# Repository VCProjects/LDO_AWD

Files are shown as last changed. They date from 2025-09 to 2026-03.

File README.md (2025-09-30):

# LDO CNC AWD Kit <sub>by Mastur_Mynd and aTinyShellScript</sub>
CNC drive frames for the [Voron Trident](https://github.com/VoronDesign/Voron-Trident) and [Voron V2.4](https://github.com/VoronDesign/Voron-2)

VT_rear_b_outer

## Key Features
* Metal! - Improved heat dissipation of stepper motors at higher current
* Shorter effective belt length between toolhead and drive gear - Improves max acceleration, input shaper results and accuracy during direction change.
* Double shear shaft support - Allows for increased tension without deflecting the drive shaft
* Backwards compatible - Toolheads or XY joints designed for the Voron Trident or Voron V2.4 will work! Keep in mind that different toolhead geometries may result in loss of travel near the front motor mounts.
* (Voron V2.4 only) Live shaft idlers - Like toothed idlers but utilizing more robust bearings for longevity

## Vendors
* [DREMC (AU)](https://store.dremc.com.au/products/ldo-voron-cnc-awd-kit-v2-4-trident)
* [3d lab tech (CA)](https://www.3dlabtech.ca/)
* [MYRIGS (FR)](https://myrigs3d.com/products/ldo-cnc-all-wheel-drive-kit-for-voron-v2-4-and-trident)
* [Partner 3D (GE)](https://partner-3d.de/)
* [Levendigs (NE)](https://levendigs.com/)
* [onetwo3D (UK)](https://www.onetwo3d.co.uk/product/ldo-voron-awd-all-wheel-drive-upgrade-kit/)
* [123-3D (UK)](https://www.123-3d.co.uk/) subsidiary of [H|2|E Commerce](https://h2ecommerce.com/)
* [Fabreeko (US)](https://www.fabreeko.com/products/ldo-cnc-all-wheel-drive-kit-for-voron-v2-4-and-trident)
* KB3D (US) [Voron Trident](https://kb-3d.com/store/voron/6134-pre-order-ldo-cnc-awd-conversion-kit-for-voron-trident-1757455457877.html) [Voron V2.4](https://kb-3d.com/store/motion/6133-pre-order-ldo-cnc-awd-conversion-kit-for-voron-v24-1757455457079.html)
* [West3D (US)](https://west3d.com/products/ldo-voron-cnc-awd-kit-v2-4-or-trident)

This kit was designed and tested in collaboration with LDO Motors. Kits produced by other manufacturers have not been vetted and may not have the same standard of quality.

## Belt Tensioning
While not required, ensuring your A and B belts are the same length will make tensioning easier.

1. Home your printer. `G28`
	* For the Voron V2 you will also need to perform a quad gantry level. `QUAD_GANTRY_LEVEL`
2. Raise the toolhead (or lower the bed) to prevent the nozzle from marring the build surface. `G0 Z+25`
3. Disable your A and B motors
   ```
   SET_STEPPER_ENABLE STEPPER=stepper_x ENABLE=0
   SET_STEPPER_ENABLE STEPPER=stepper_x1 ENABLE=0
   SET_STEPPER_ENABLE STEPPER=stepper_y ENABLE=0
   SET_STEPPER_ENABLE STEPPER=stepper_y1 ENABLE=0
   ```
4. Loosen the grub screws holding the front drive pulleys to the motor shaft. Ensure that the pulleys are able to move freely from the shaft.
5. Move your toolhead to the center of the bed
6. Adjust tension on each belt path using the M5 SHCS in the tensioner block. Try to adjust tension evenly across the two belt paths, reducing adjustments as you get closer to your desired tension
7. Move the toolhead in the X and Y directions to make sure it is moving freely.
8. Enable your A and B motors. This will send them to the nearest full step which will sync the motors and pulleys in the next step.
   ```
   SET_STEPPER_ENABLE STEPPER=stepper_x ENABLE=1
   SET_STEPPER_ENABLE STEPPER=stepper_x1 ENABLE=1
   SET_STEPPER_ENABLE STEPPER=stepper_y ENABLE=1
   SET_STEPPER_ENABLE STEPPER=stepper_y1 ENABLE=1
   ```
9. Tighten the grub screws holding the front drive pulleys to the motor shaft. Ensure that none of the grub screws are along the flat when using a D cut shaft motor.

## Credit and Attribution
**Lead Designer**\
Mastur_Mynd

**Lead Design Consultant**\
aTinyShellScript

**Project Coordinator**\
JasonFromLDO

**Design Consultant**\
CameronFromLDO\
DaveFromLDO

**Production**\
LDO Motors

**Testing**\
hartk\
JoseFromLDO us\
joshmurrah\
Kittie Katt\
Reth\
ThessienDSD

**Base Design**\
Voron Design Team

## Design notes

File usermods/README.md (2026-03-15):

# Mods by users - For users
This section houses creations from users that have either made assembly easier, improved functionality or just look too-darn-cool!

## Requirements
* All mods must abide by GPLv3 licensing standards. This means the CAD document (preferably .STEP format) must be included along with printable STL files. Additionally, attribution must be provided if an external source file was used (all mods here are assumed to derrive from the kits, no attribution to these kits are necessary).
* All STL files are expected to be print ready, meaning their orientation should not need to change after importing into the users' preferred slicer.
* Include some images of the finished product. This can either be a render or a photo of a printed part
* Include a BOM (bill of materials) and note whether or not the required hardware was already included in the kit.
* If the mod changes, removes, or improves functionality, please describe how it does so
* If the mod is a complex change you'll need to include documentation in some form on how to install your mod.
* Kit compatability should use the following: `:heavy_check_mark:` for compatible,`:x:` for NOT compatible and `:grey_question:` for unknown compatability

| Author | Mod Name | V2 AWD | V2 2WD | VT AWD | VT 2WD |
|---|---|---|---|---|---|
| Mastur_Mynd | [Y Endstop Mount](./Mastur_Mynd/Y_Endstop_Mount) | :heavy_check_mark: | :heavy_check_mark: | :heavy_check_mark: | :heavy_check_mark: |
| Kyle_GB| [Accent Sleeves](./Kyle_GB/Accent_Sleeves) | :heavy_check_mark: | :heavy_check_mark: | :heavy_check_mark: | :heavy_check_mark: |
| TheSin- | [AABB Microfit3 Pods](./TheSin-/AABB_Microfit3_Pods) | :heavy_check_mark: | :x: | :x: | :x: |
| TheSin- | [Front Motor Wiring](./TheSin-/Front_Motor_Wiring) | :heavy_check_mark: | :x: | :x: | :x: |
| TheSin- | [Zumbilical](./TheSin-/Zumbilical) | :heavy_check_mark: | :heavy_check_mark: | :x: | :x: |

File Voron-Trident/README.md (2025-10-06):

# LDO CNC AWD Kit <sub>by Mastur_Mynd and aTinyShellScript</sub>
CNC drive frames designed specifically for your [Voron Trident](https://github.com/VoronDesign/Voron-Trident)

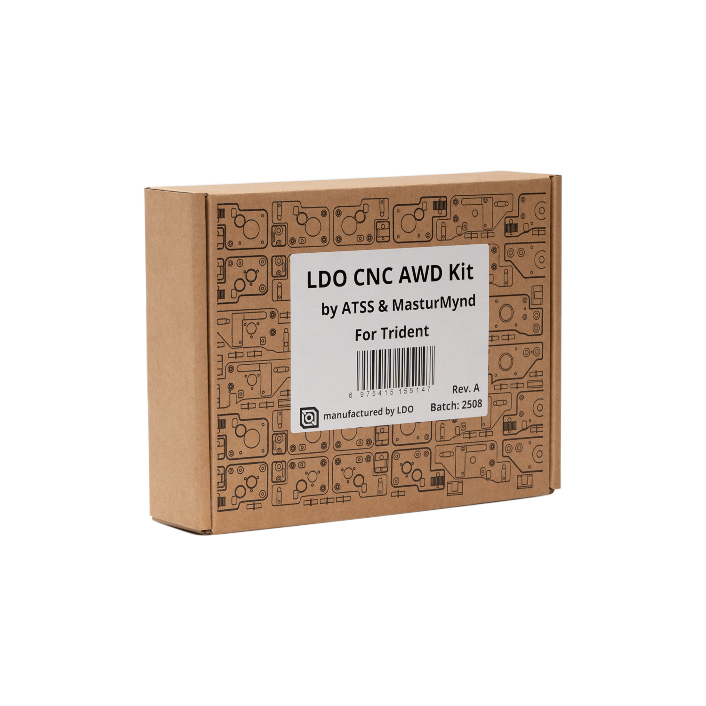
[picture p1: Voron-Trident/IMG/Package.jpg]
Package


## Things to consider
There are a few printed parts recommended for clean cable management. Head over to the STL directory to download these files and print what you'll need before prepping for installation.

It is recommended to get some channel covers for your front corner extrusions to hide the front motor wires on their way to the electronics bay.

Depending on the orientation of the front motor mounts and the toolhead assembly, some amount of printable area will be lost at the front corners of the build plate. The below table will be updated as data comes in. If you would like to contribute to this table please submit a pull request or create an issue with dimensions for both the Voron Trident and the Voron V2.4r2.

---
| Toolhead | X Loss (mm) | Y Loss (mm) |
| --- | --- | --- |
| Stealthburner | 17.8 | 47.6 |

## So what's in the box?!
Note that the Contents section of the [assembly manual](assembly_manual.pdf) accounts for individual hardware components. For an improved assembly experience some components are preinstalled.

---
| Qty | Part Name | Image |
| --- | --- | --- |
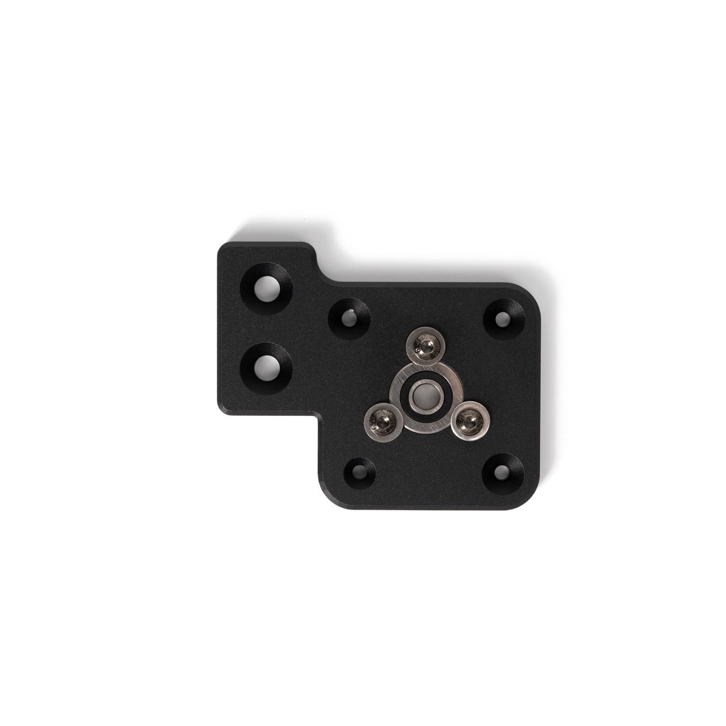
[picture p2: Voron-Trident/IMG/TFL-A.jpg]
TFL-A
| 1 | Front A Drive Frame Lower |  |
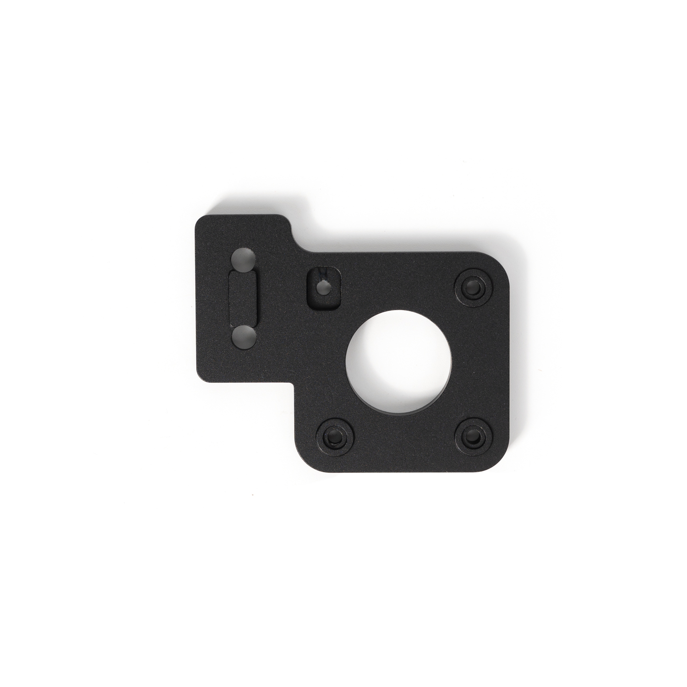
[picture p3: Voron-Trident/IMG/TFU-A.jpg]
TFU-A
| 1 | Front A Drive Frame Upper |  |
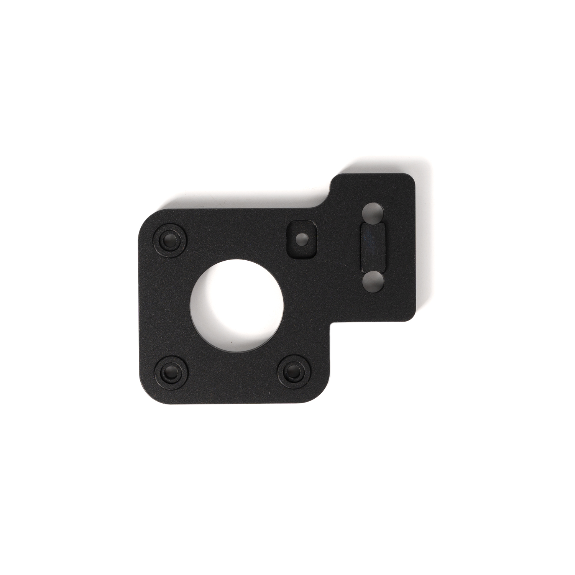
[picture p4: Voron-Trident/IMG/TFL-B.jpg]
TFL-B
| 1 | Front B Drive Frame Lower |  |
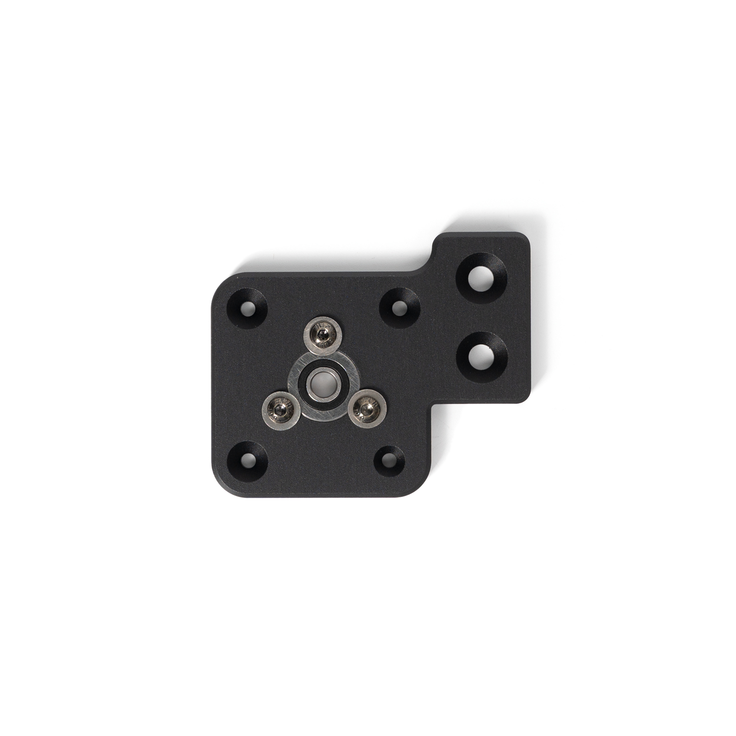
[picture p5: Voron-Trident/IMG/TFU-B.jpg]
TFU-B
| 1 | Front B Drive Frame Upper |  |
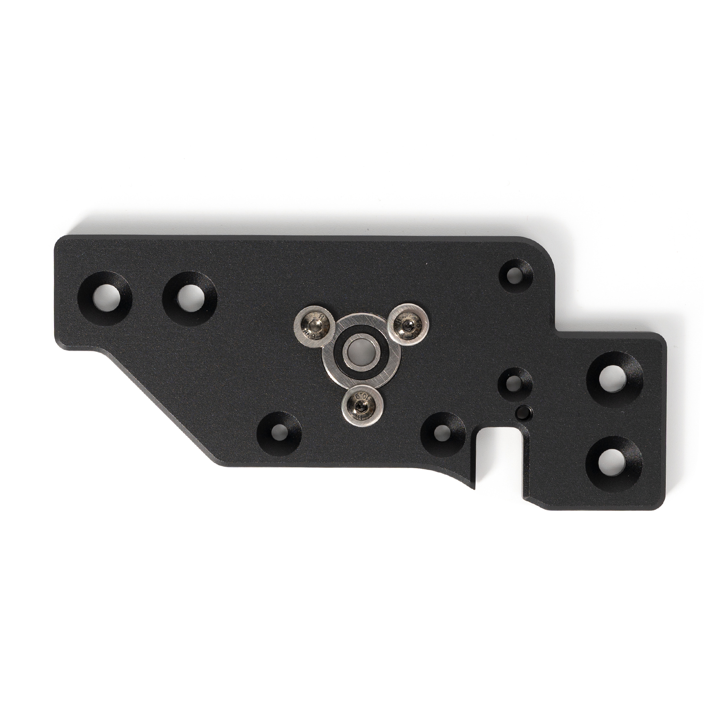
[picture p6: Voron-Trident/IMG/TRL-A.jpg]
TRL-A
| 1 | Rear A Drive Frame Lower |  |
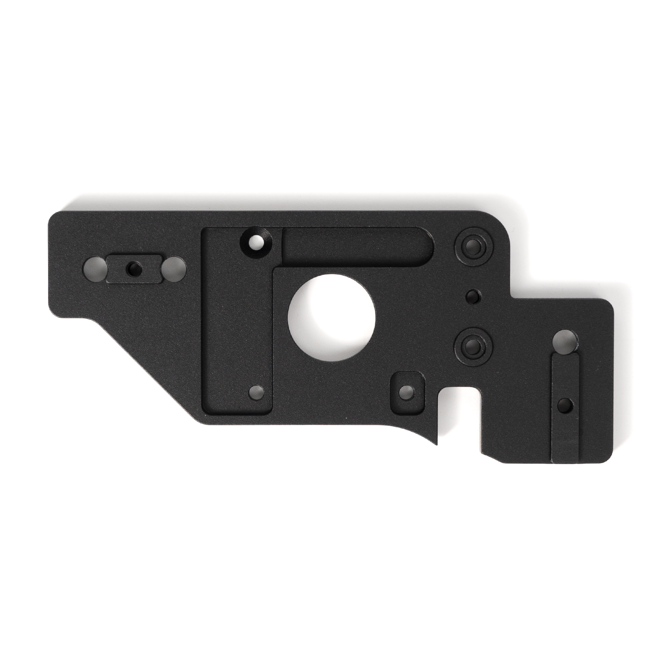
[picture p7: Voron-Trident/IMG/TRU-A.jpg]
TRU-A
| 1 | Rear A Drive Frame Upper |  |
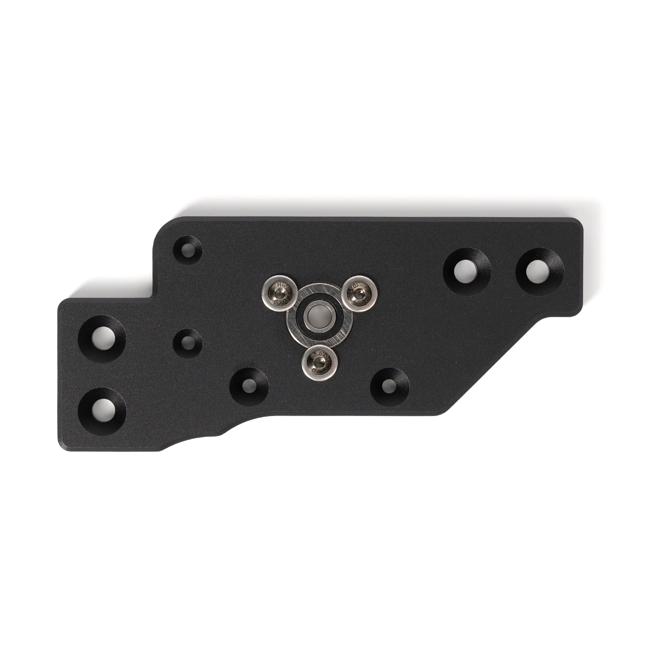
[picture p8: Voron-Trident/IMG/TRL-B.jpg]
TRL-B
| 1 | Rear B Drive Frame Lower |  |
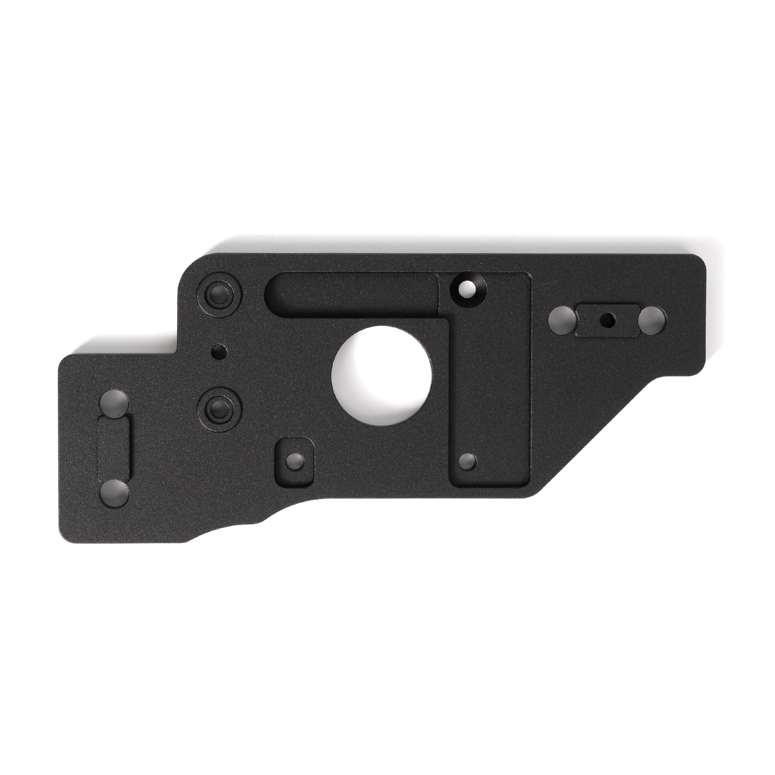
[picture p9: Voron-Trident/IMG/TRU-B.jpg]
TRU-B
| 1 | Rear B Drive Frame Upper |  |
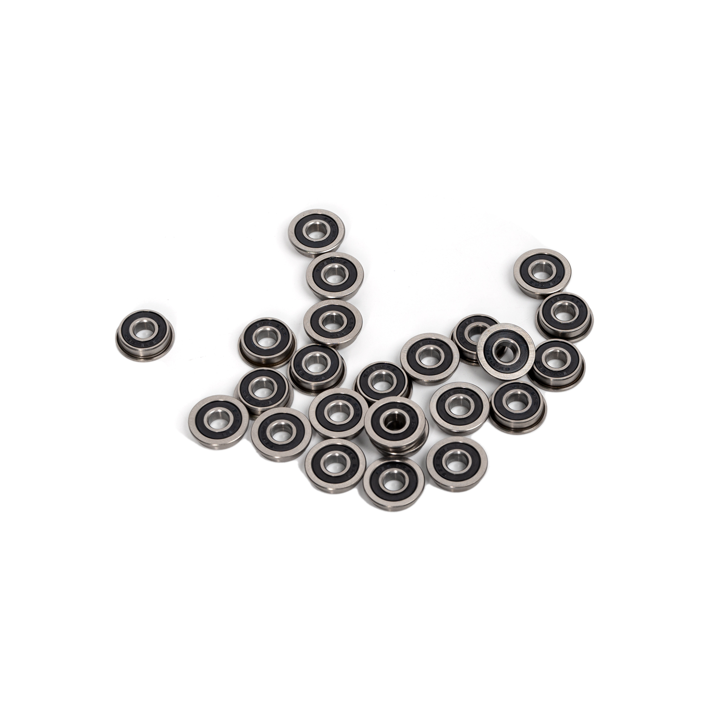
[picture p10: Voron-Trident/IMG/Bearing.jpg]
Bearing
| 24 | F695-2RS Bearing |  |
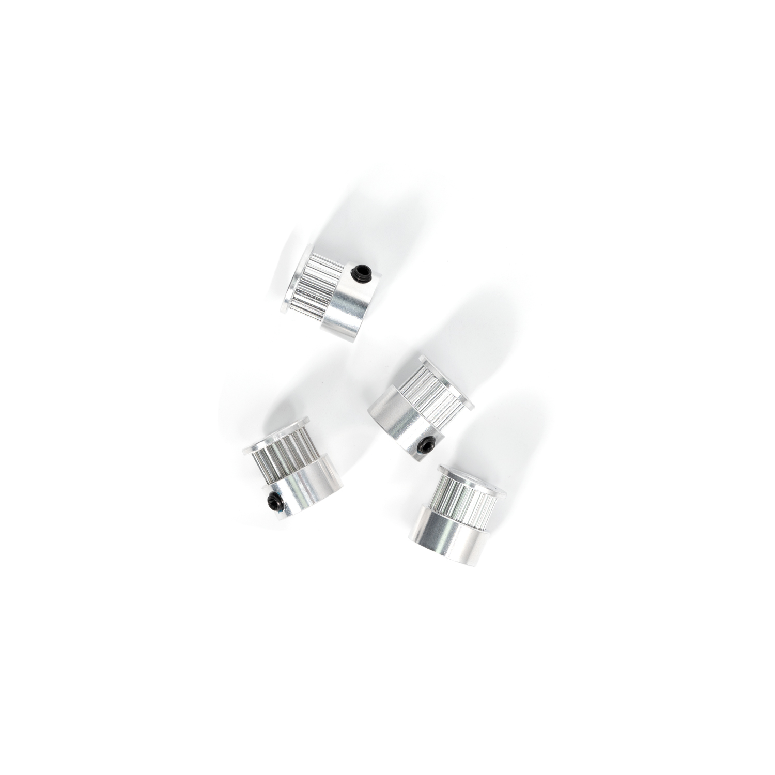
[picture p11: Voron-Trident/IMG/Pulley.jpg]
Pulley
| 4 | Pulley |  |
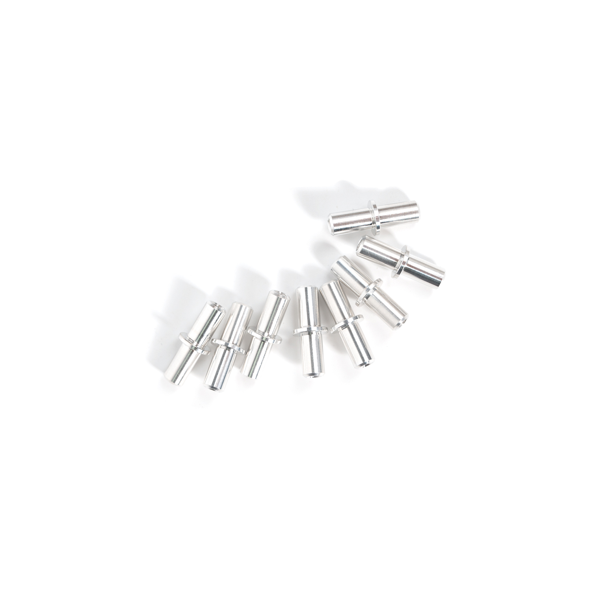
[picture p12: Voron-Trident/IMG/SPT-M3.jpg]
SPT-M3
| 8 | Shim Pin - Threaded (M3) |  |
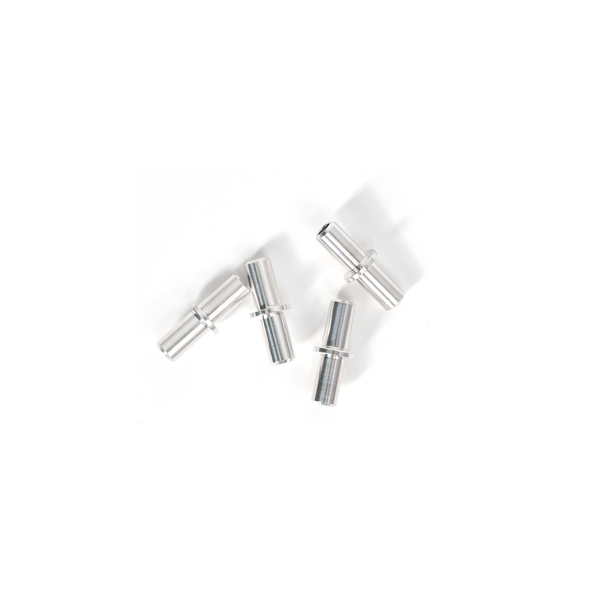
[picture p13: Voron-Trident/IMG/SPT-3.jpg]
SPT-3
| 4 | Shim Pin - Unthreaded |  |
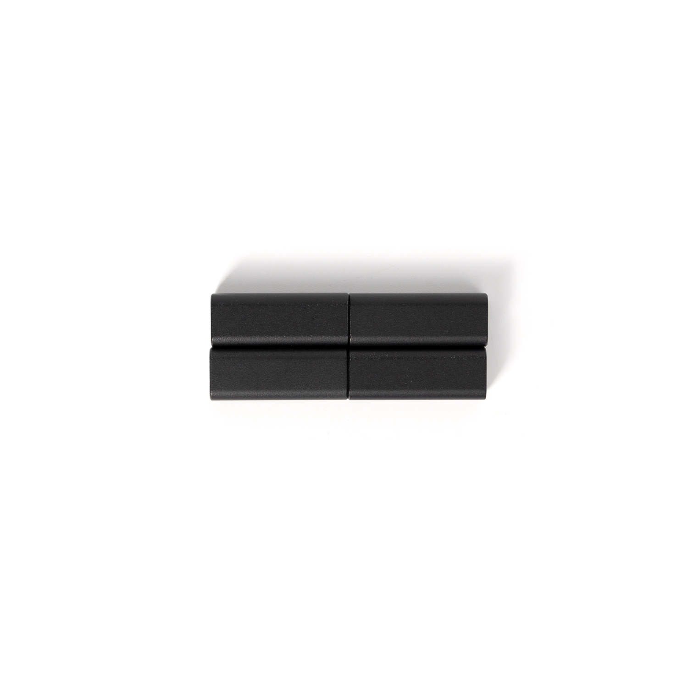
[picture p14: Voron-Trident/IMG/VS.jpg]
VS
| 4 | Standoff |  |
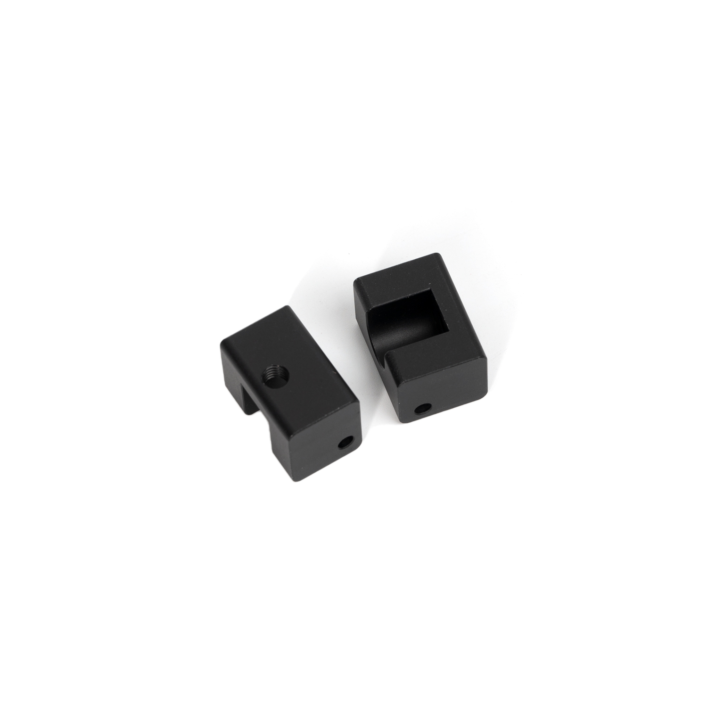
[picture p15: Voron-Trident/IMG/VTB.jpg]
VTB
| 2 | Tensioner Block |  |
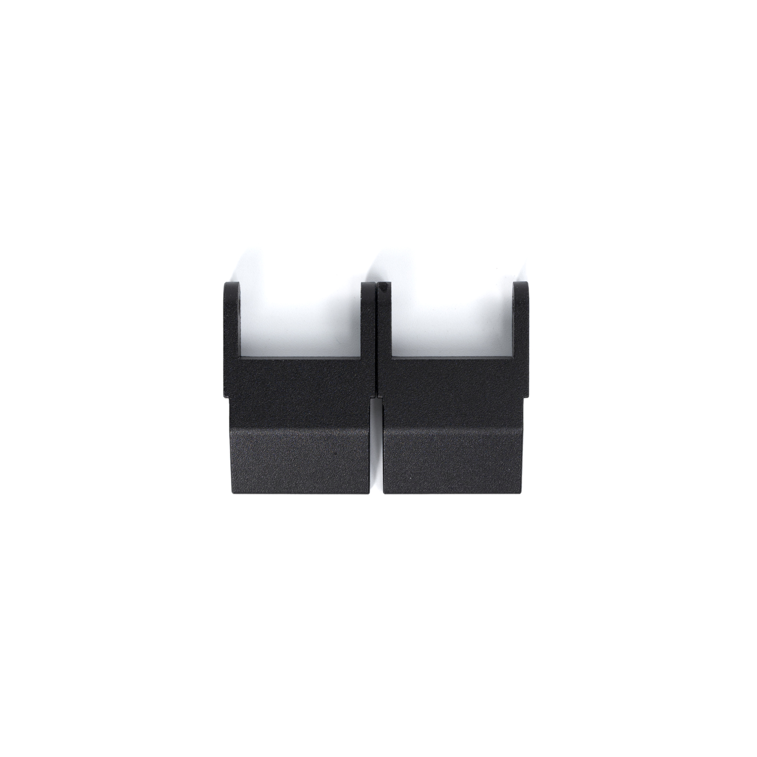
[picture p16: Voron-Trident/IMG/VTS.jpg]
VTS
| 2 | Tensioner Slide |  |
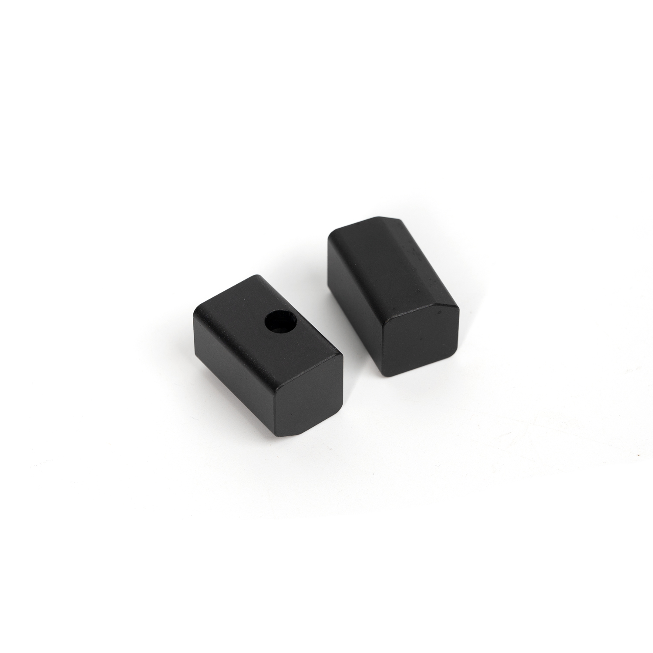
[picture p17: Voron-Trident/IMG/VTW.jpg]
VTW
| 2 | Tensioner Wedge |  |
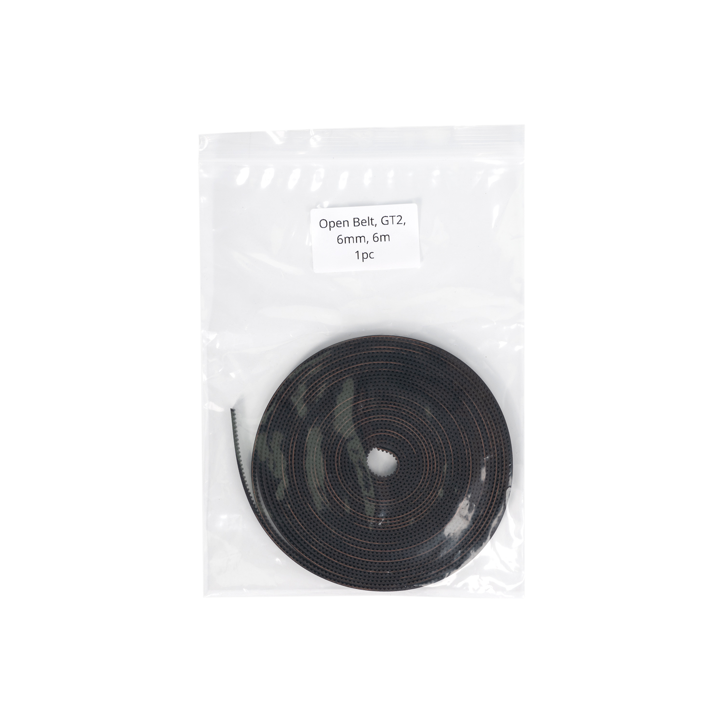
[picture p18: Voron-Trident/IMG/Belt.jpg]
Belt
| 6m | Open Belt, GT2, 6mm |  |
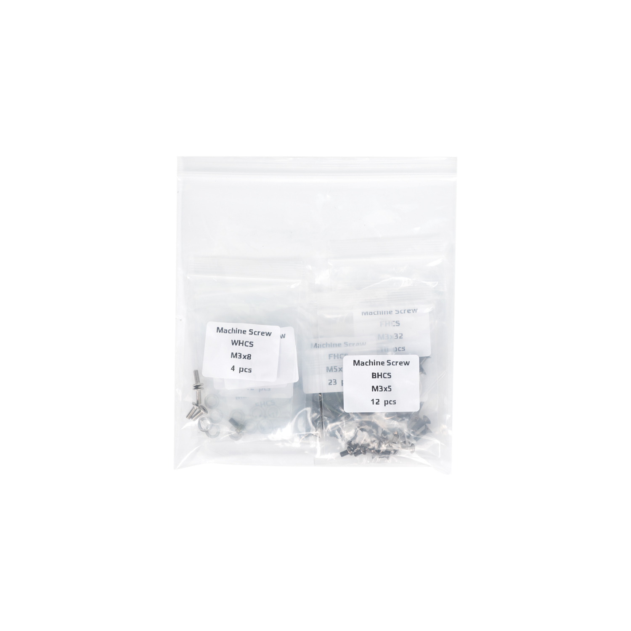
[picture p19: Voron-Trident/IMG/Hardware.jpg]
Hardware
| | All hardware necessary to assemble |  |

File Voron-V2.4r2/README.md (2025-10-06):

# LDO CNC AWD Kit <sub>by Mastur_Mynd and aTinyShellScript</sub>
CNC drive frames designed specifically for your [Voron V2.4](https://github.com/VoronDesign/Voron-2)

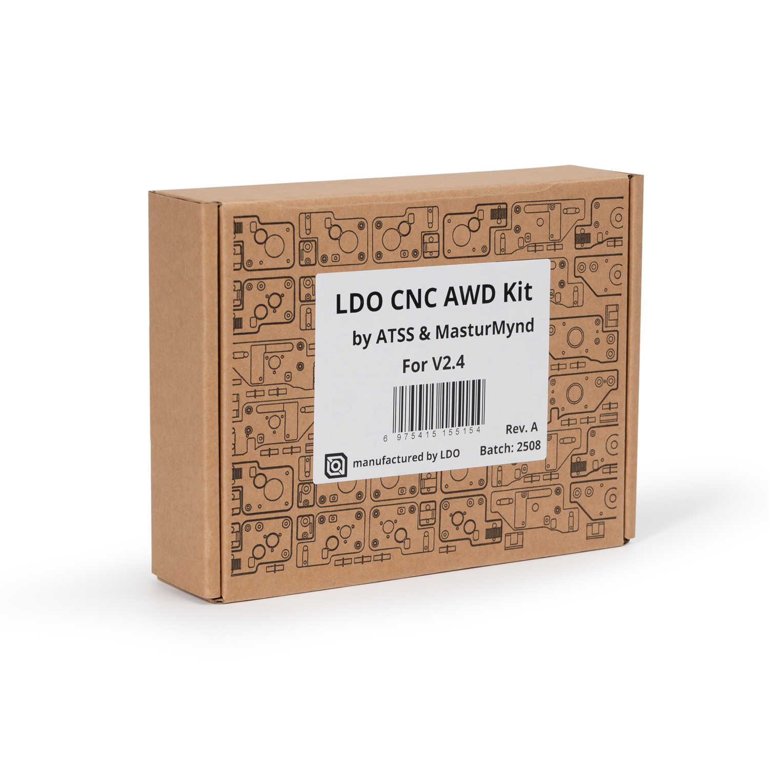
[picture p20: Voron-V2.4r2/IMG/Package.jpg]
Package


## Things to consider
There are a few printed parts recommended for clean cable management. Head over to the STL directory to download these files and print what you'll need before prepping for installation.

It is recommended to get some channel covers for your Y extrusions. This will prevent the motor wires from rubbing against the belts.

Depending on the orientation of the front motor mounts and the toolhead assembly, some amount of printable area will be lost at the front corners of the build plate. The below table will be updated as data comes in. If you would like to contribute to this table please submit a pull request or create an issue with dimensions for both the Voron Trident and the Voron V2.4r2.

---
| Toolhead | X Loss (mm) | Y Loss (mm) |
| --- | --- | --- |
| Stealthburner | 35.9 | 48.6 |

## So what's in the box?!
Note that the Contents section of the [assembly manual](assembly_manual.pdf) accounts for individual hardware components. For an improved assembly experience some components are preinstalled.

---
| Qty | Part Name | Image |
| --- | --- | --- |
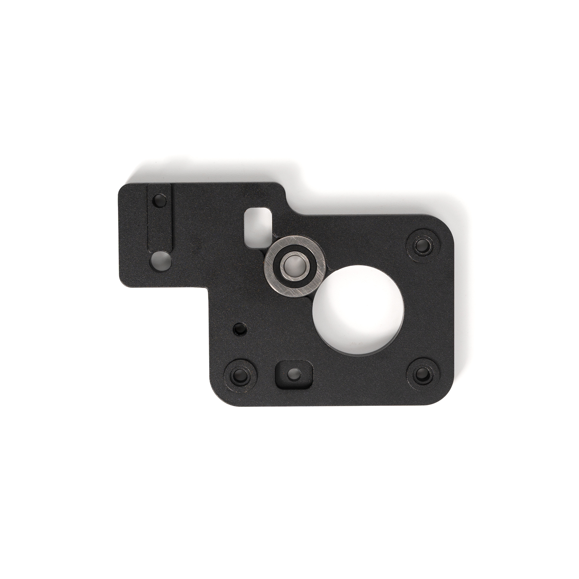
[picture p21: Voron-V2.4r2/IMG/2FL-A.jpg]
2FL-A
| 1 | Front A Drive Frame Lower |  |
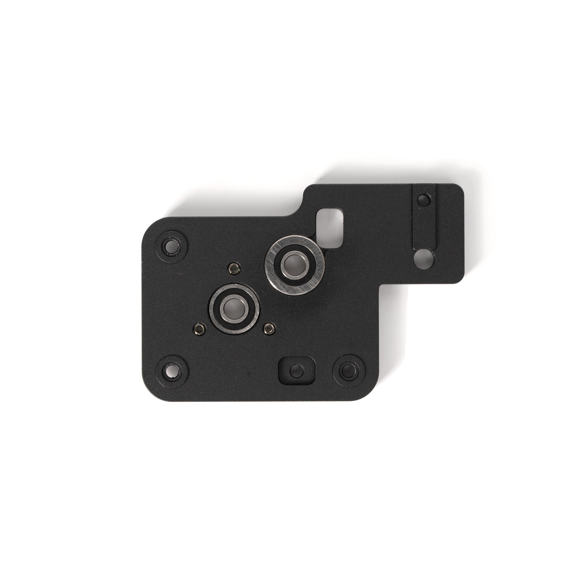
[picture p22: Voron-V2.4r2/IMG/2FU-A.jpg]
2FU-A
| 1 | Front A Drive Frame Upper |  |
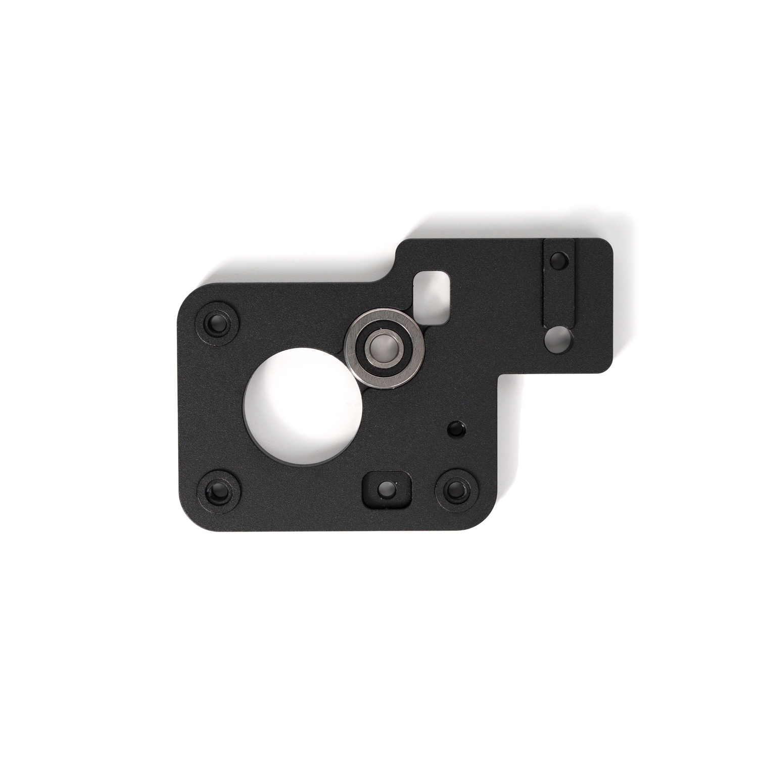
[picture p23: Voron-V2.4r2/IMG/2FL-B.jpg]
2FL-B
| 1 | Front B Drive Frame Lower |  |
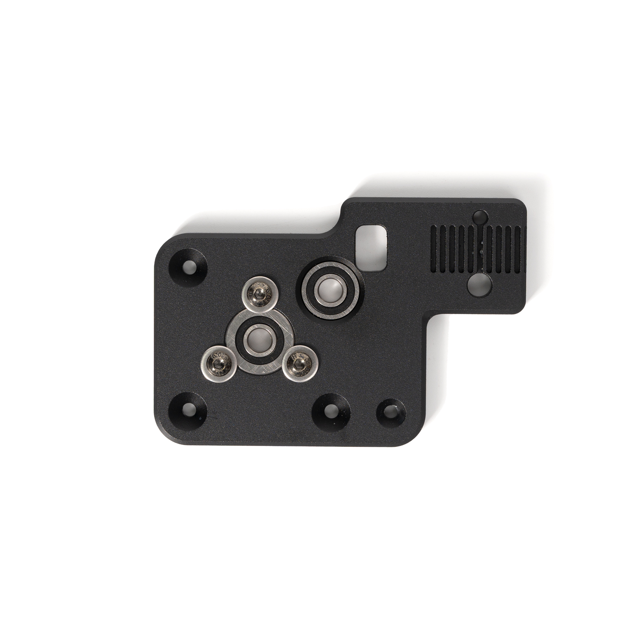
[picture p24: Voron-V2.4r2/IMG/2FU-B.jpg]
2FU-B
| 1 | Front B Drive Frame Upper |  |
| 1 | Rear A Drive Frame Lower | 2RL-A |
| 1 | Rear A Drive Frame Upper | 2RU-A |
| 1 | Rear B Drive Frame Lower | 2RL-B |
| 1 | Rear B Drive Frame Upper | 2RU-B |
| 26 | F695-2RS Bearing | Bearing |
| 6 | Pulley | Pulley |
| 8 | Shim Pin - Threaded (M3) | SPT-M3 |
| 4 | Shim Pin - Unthreaded | SPT-3 |
| 4 | Belt Clamp A | VBC-A |
| 4 | Belt Clamp B | VBC-B |
| 4 | Standoff | VS |
| 2 | Tensioner Block | VTB |
| 2 | Tensioner Slide | VTS |
| 2 | Tensioner Wedge | VTW |
| 6m | Open Belt, GT2, 6mm | Belt |
| | All hardware necessary to assemble | Hardware |

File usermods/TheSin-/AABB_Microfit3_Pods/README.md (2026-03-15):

# AABB Microfit3 Pods
Add microfit3 quick connections for AABB motors.

render

## BOM AWD
| Part | Quantity | Kit Included |
|---|---|---|
| [a]_AABB_Connector_Plug_Microfit.stl | 2 | :x: |
| MicroFit3 2x2 Male w/pin (0430250400) | 4 | :x: |
| MicroFit3 2x2 Female w/pin (0430200409) | 4 | :x: |
| M3x10 SHCS | 2 | :x: |
| M3 Roll-in or hammer nut | 2 | :x: |
| OPTIONAL Ziptie (4mm wide) | 2 | :x: |

I used some extrusion covers from [Front Motor Wiring](../Front_Motor_Wiring) to clean up the wires on the rear x beam

## Credits
The base shape was based on someone else's design but I can't find it in my fiels to give them the proper credits.  It might have been [Ramalama2 AB_Plugs](https://github.com/Ramalama2/Voron-2-Mods/tree/main/AB_Plugs).

## Photos
render

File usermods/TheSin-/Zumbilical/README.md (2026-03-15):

# Zumbilical
Add Zumbilical to replace the Z Chain.  Also made the top piece modular so you can create a PUG version if you'd prefer that.

render

## BOM
| Part | Quantity | Kit Included |
|---|---|---|
| [a]_horizontal_chain_upper_mount.stl | 1 | :x: |
| [a]_horizontal_chain_lower_mount_PG9.stl | 1 | :x: |
| [a]_horizontal_chain_upper_mount.stl | 1 | :x: |
| PG9 glands | 2 | :x: |
| M3x8 BHCS or SHCS | 3 | :x: |
| M5x8 BHCS | 3 | :x: |
| M3 Heatset | 3 | :x: |
| M5 Roll-in or hammer nut | 3 | :x:|
| OPTIONAL Ziptie (4mm) | 2 | :x: |
| OPTIONAL Wire sleeve (recommended) | length of your zumbilical | :x: |
| **OPTIONAL Fence, but recommended** | | |
| [a]_fence_mount_left.stl | 1 | :x: |
| [a]_fence_mount_right.stl | 1 | :x: |
| [a]_fence.stl | 1 | :x: |
| M3x6 BHCS | 2 | :x: |
| M5x8 BHCS | 2 | :x: |
| M3 Heatset | 2 | :x: |
| M5 roll-in or hammer nut | 2 | :x: |
| **OPTIONAL Y cable cover** | |
| [a]_gantry_cable_cover | Replaces the kit verison | :x: |
| Same screws as kit version | | :heavy_check_mark: |

## Photos
render

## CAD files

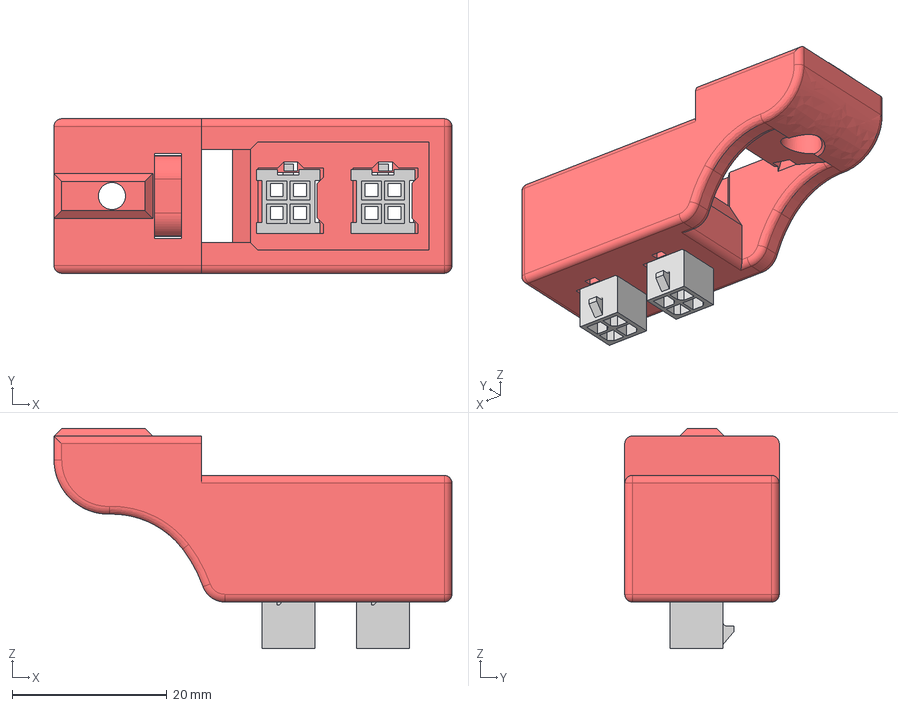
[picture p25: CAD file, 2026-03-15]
usermods/TheSin-/AABB_Microfit3_Pods/CAD/AABB_Connector_Plug_Microfit.step
51.5 x 20.0 x 28.5 mm
MainBody

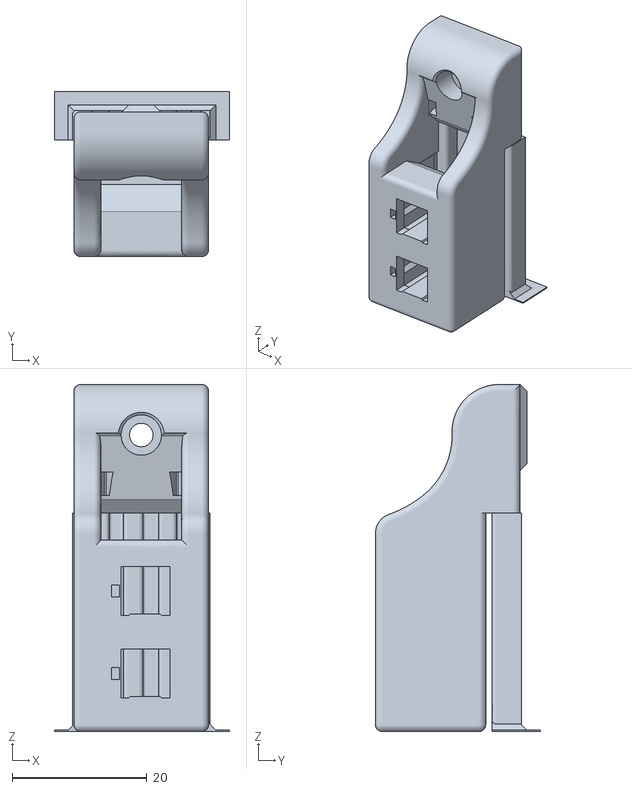
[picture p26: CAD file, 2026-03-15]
usermods/TheSin-/AABB_Microfit3_Pods/STL/[a]_AABB_Connector_Plug_Microfit.stl
26.0 x 24.5 x 51.5

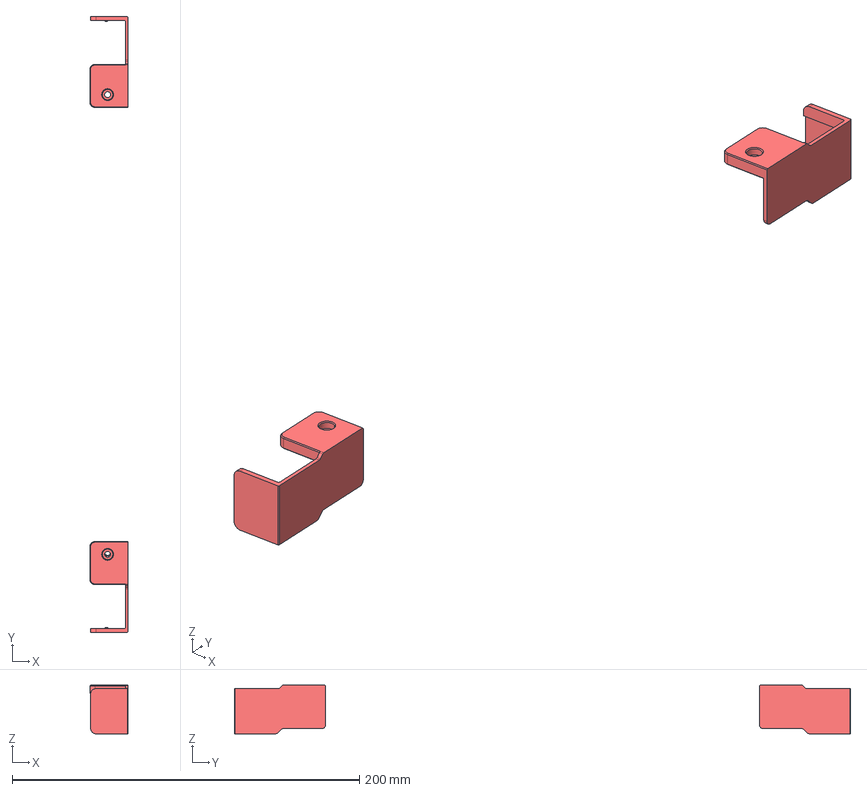
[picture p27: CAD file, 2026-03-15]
usermods/TheSin-/Front_Motor_Wiring/CAD/Front_Wiring_Covers.step
22.1 x 354.8 x 28.0 mm
[a]_wiring_side_a_x2
[a]_wiring_side_b_x2
M3 Roll-In T Nut

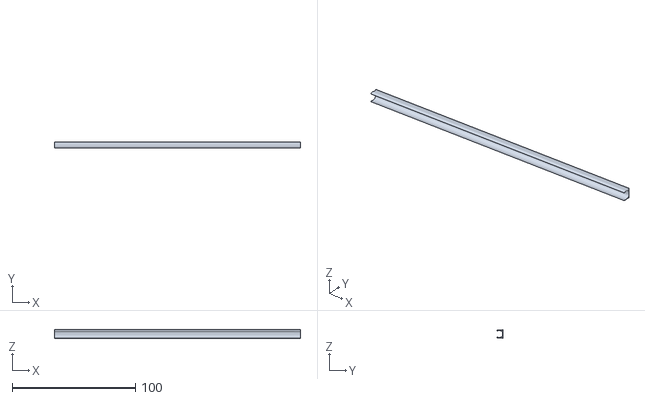
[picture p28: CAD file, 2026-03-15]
usermods/TheSin-/Front_Motor_Wiring/STL/Extrusion_Cover.stl
200.0 x 5.10 x 7.00

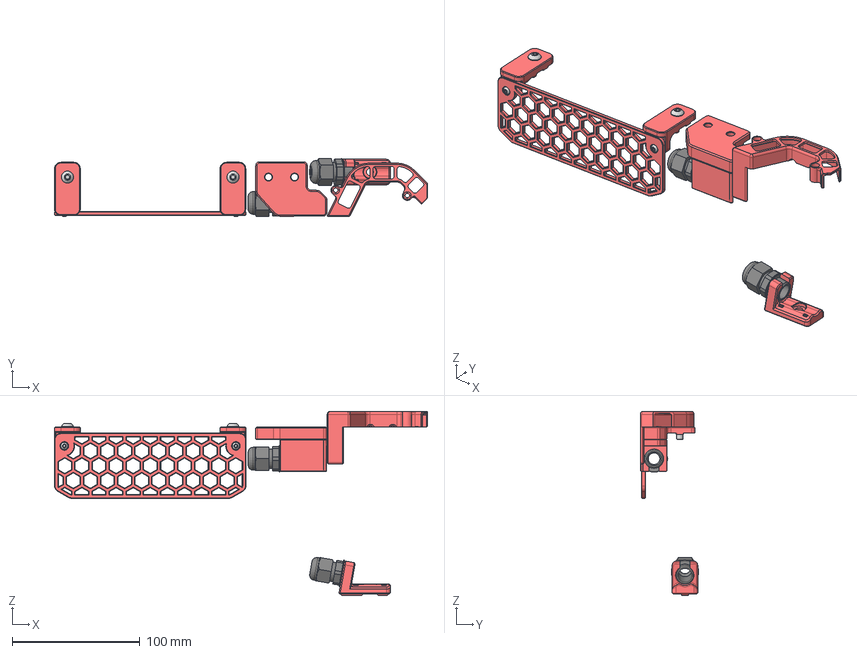
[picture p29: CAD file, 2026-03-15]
usermods/TheSin-/Zumbilical/CAD/Zumbilical.step
292.1 x 45.7 x 144.1 mm
VORON2.4_Assembly_Gantry_Cable Cover
[a]_PG9_adaptor_3_hole
[a]_horizontal_chain_upper_mount
[a]_horizontal_chain_lower_mount_PG9
[a]_fence_mount_left
[a]_fence_mount_right
[a]_fence
(Unsaved) x 2
M3x8 BHCS x 2
M5x10 BHCS x 2

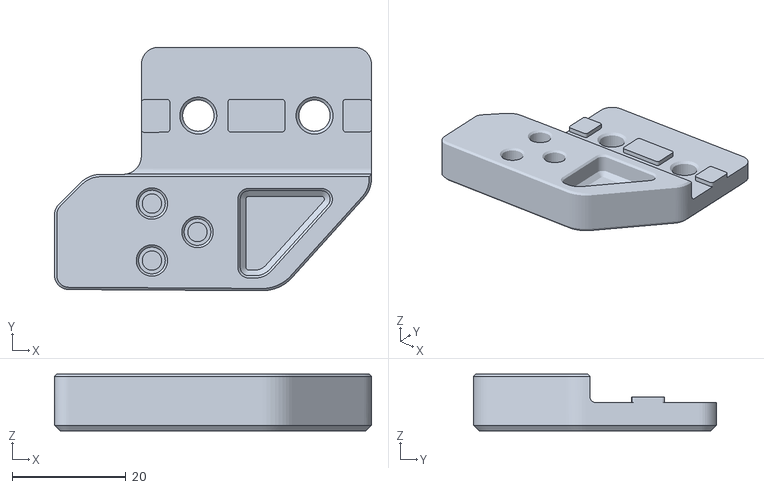
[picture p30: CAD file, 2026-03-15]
usermods/TheSin-/Zumbilical/STL/[a]_horizontal_chain_upper_mount.stl
55.7 x 42.7 x 10.00

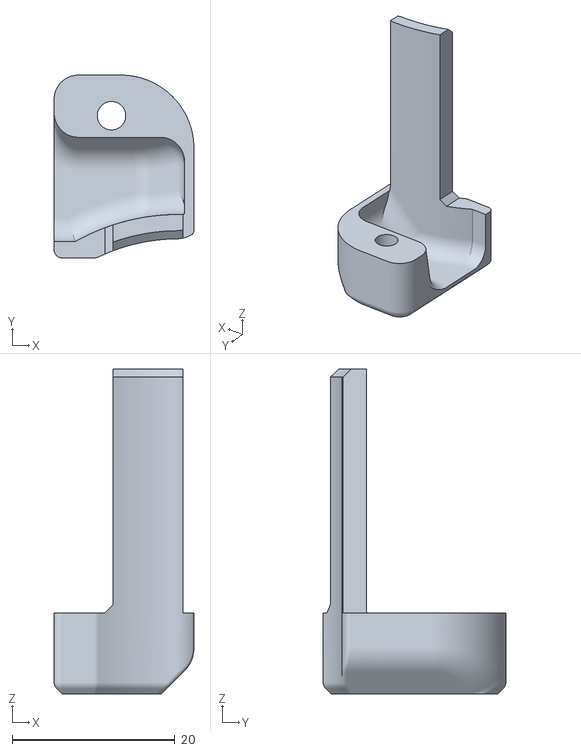
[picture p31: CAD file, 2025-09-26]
Voron-Trident/STL/[a]_wire_cover.stl
17.2 x 22.5 x 40.0

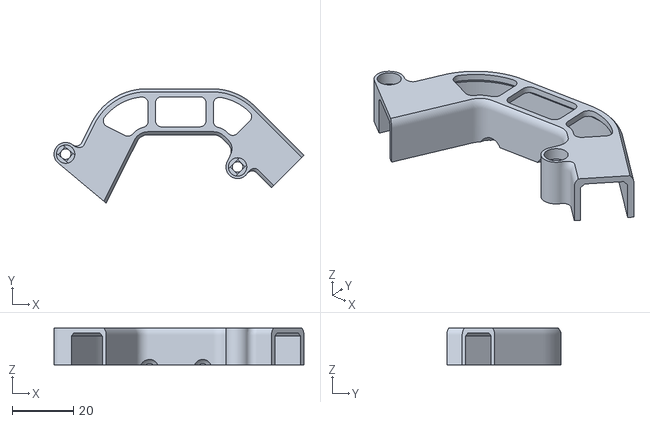
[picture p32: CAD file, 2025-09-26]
Voron-V2.4r2/STL/[a]_cable_cover.stl
81.5 x 37.3 x 12.0

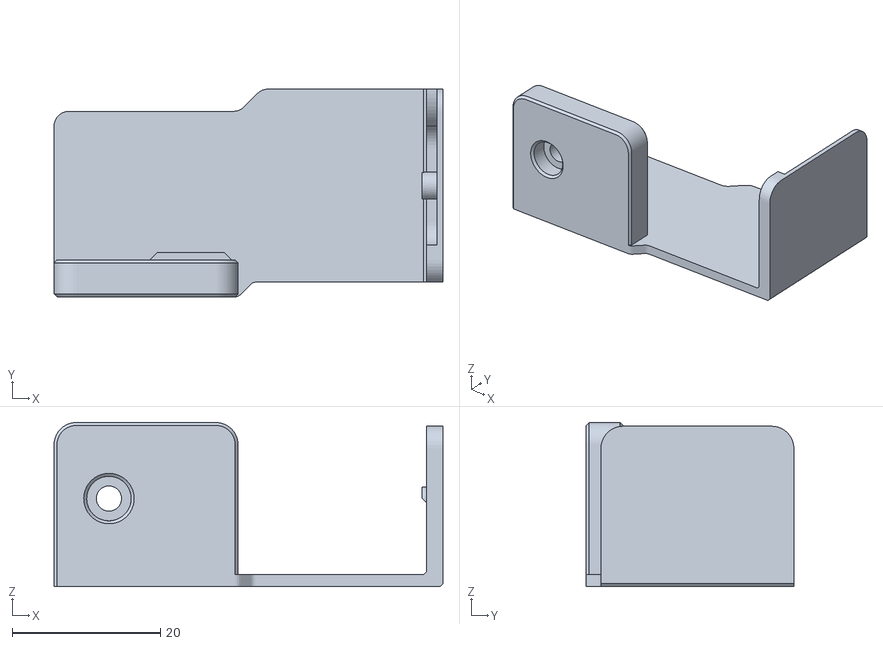
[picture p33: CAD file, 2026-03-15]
usermods/TheSin-/Front_Motor_Wiring/STL/[a]_wiring_side_a_x2.stl
52.4 x 28.0 x 22.1

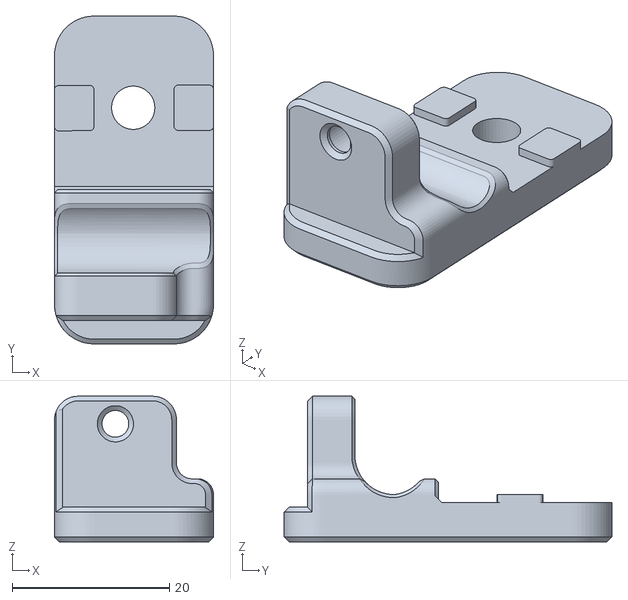
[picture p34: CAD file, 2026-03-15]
usermods/TheSin-/Zumbilical/STL/[a]_fence_mount_left.stl
20.2 x 41.6 x 18.5

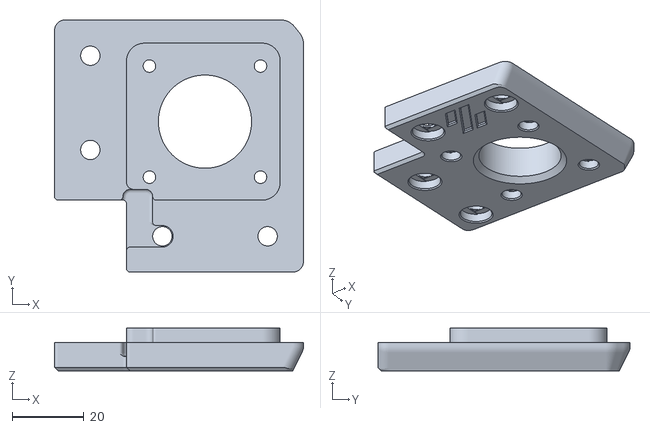
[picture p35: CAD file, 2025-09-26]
Voron-Trident/STL/z_stepper_right.stl
69.5 x 70.4 x 12.0

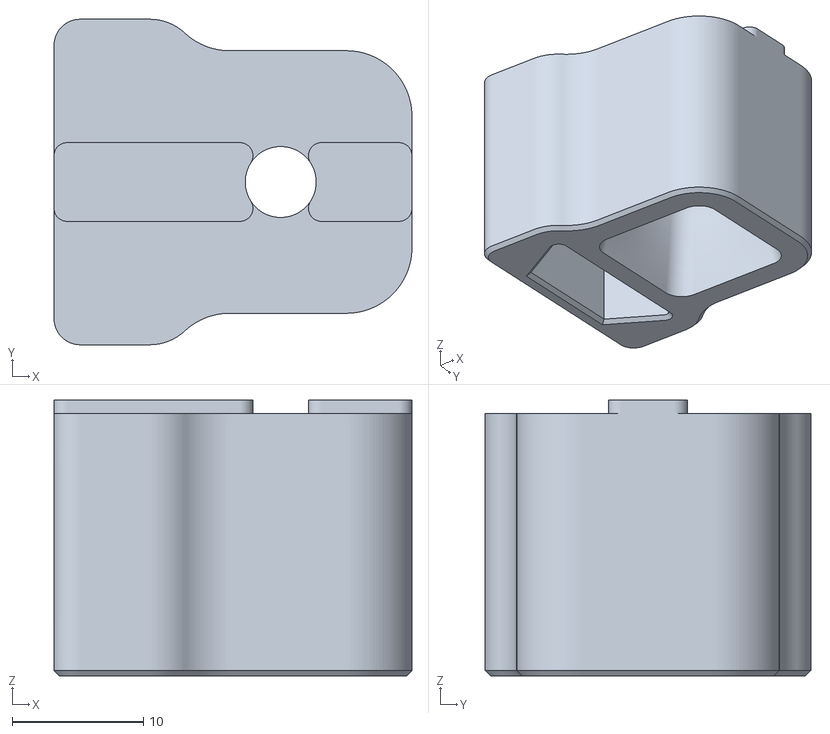
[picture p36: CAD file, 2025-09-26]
Voron-V2.4r2/STL/z_chain_upper_mount.stl
27.3 x 24.8 x 21.0

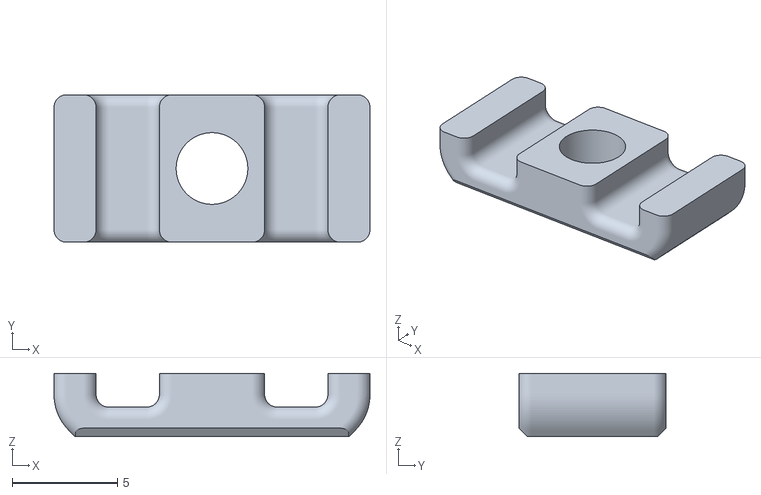
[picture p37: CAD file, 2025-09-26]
Voron-V2.4r2/STL/[a]_cable_anchor_x6.stl
15.0 x 7.00 x 3.00

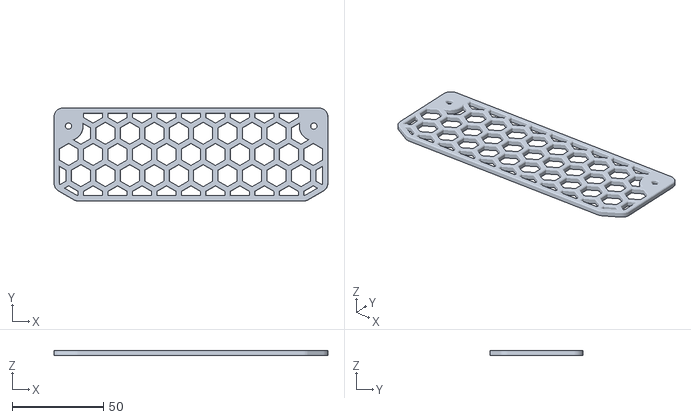
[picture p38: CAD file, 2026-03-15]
usermods/TheSin-/Zumbilical/STL/[a]_fence.stl
150.0 x 51.0 x 3.00

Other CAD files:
usermods/TheSin-/Front_Motor_Wiring/STL/[a]_wiring_side_b_x2.stl
usermods/TheSin-/Zumbilical/STL/[a]_fence_mount_right.stl
Voron-Trident/STL/z_stepper_left.stl
usermods/TheSin-/Zumbilical/STL/[a]_PG9_adaptor_3_hole.stl
usermods/TheSin-/Zumbilical/STL/[a]_gantry_cable_cover.stl
usermods/TheSin-/Zumbilical/STL/[a]_horizontal_chain_lower_mount_PG9.stl

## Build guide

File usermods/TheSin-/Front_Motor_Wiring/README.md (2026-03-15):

# Front Motor Wiring Covers
Adds some protection and cleans up wiring for the front motors.

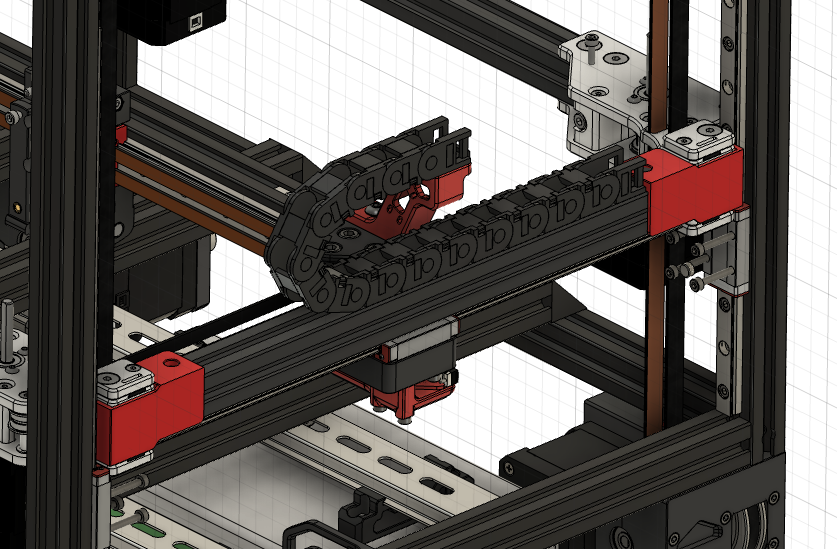
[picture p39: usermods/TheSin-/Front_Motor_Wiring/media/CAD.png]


## BOM AWD
| Part | Quantity | Kit Included |
|---|---|---|
| [a]_wiring_side_a_x2.stl | 2 | :x: |
| [a]_wiring_side_b_x2.stl | 2 | :x: |
| Extrusion_Cover.stl | scale to fit the gap | :x: |
| M3x8 SHCS | 4 | :x: |
| M3 Roll-in or hammer nut | 4 | :x: |

## Credits
Extrusion_Cover.stl was not designed by me, sadly I've had it so long I can not give proper credits as I can't remember where it's from.  But the print orientation isn't correct. There are many options, this is just the one I used so I included it.

## Photos
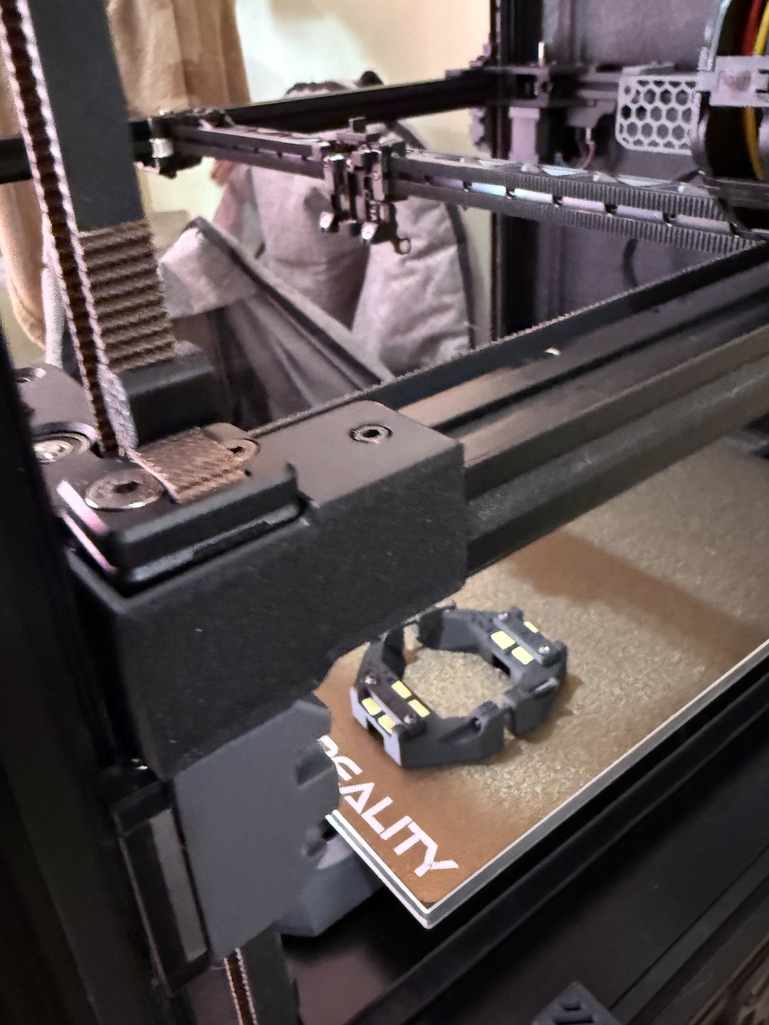
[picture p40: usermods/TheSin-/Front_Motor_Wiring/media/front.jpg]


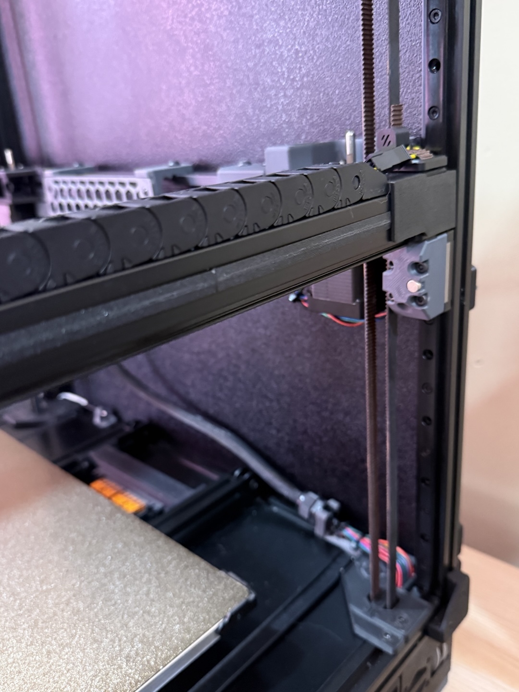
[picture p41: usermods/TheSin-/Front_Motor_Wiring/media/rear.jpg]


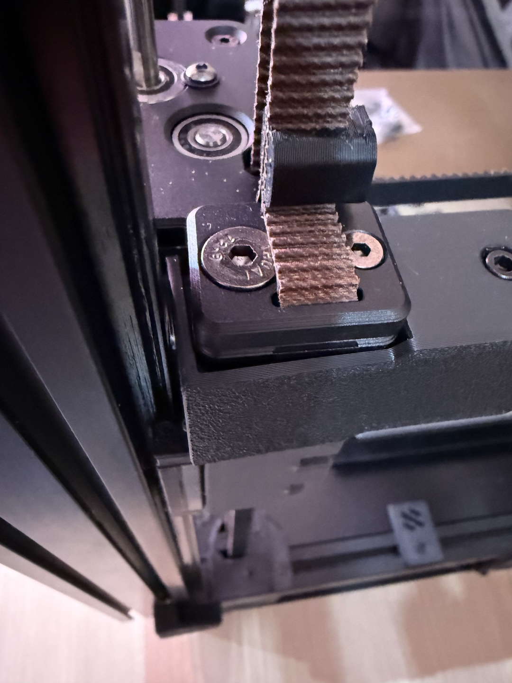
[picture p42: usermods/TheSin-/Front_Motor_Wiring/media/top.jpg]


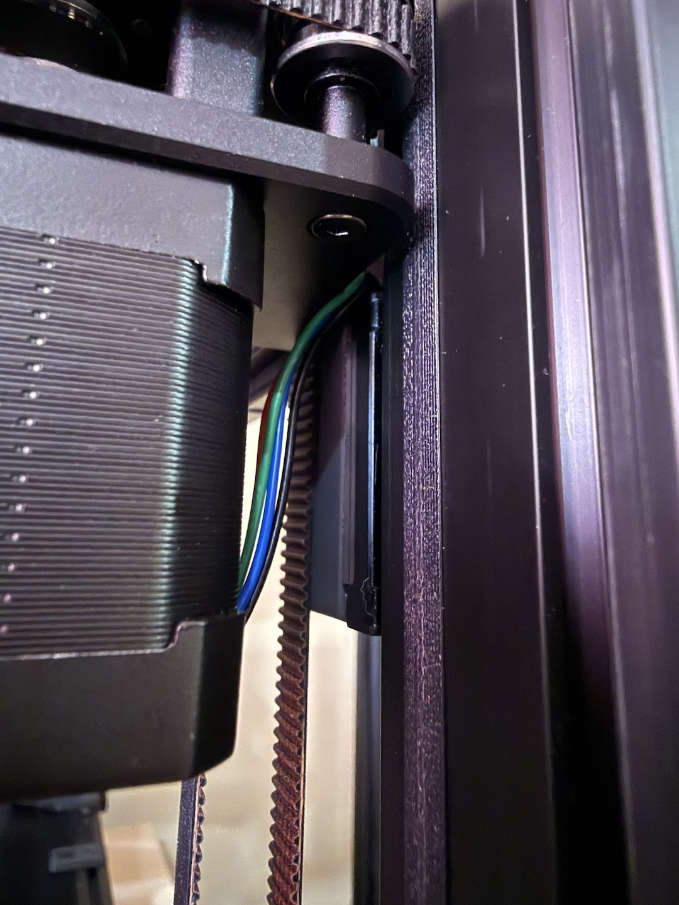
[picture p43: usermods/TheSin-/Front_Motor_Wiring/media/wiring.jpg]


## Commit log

2025-09-26 Public Release
    [[a]_cable_anchor_x6.stl, [a]_cable_cover.stl, [a]_wire_cover.stl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]
2025-09-27 Manual Corrections
    Per https://github.com/VCProjects/LDO_AWD/issues/2
    There were some issues with callouts in the assembly manuals. The mentioned issues along with other issues identified during review have been corrected. Additionally, notes related to preinstalled F695-2RS bearings have been added for LDO kits.
2025-10-06 Added tables for build area loss
    Depending on the orientation of the front motor mounts and the toolhead assembly, some amount of printable area will be lost at the front corners of the build plate.
2026-03-01 Corrected Contents and Headers
    The contents section had the wrong images for the drive frame plates. Headers for A / B sections were reversed.
